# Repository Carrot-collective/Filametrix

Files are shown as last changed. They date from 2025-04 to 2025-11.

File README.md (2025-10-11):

## Carrot Collective Projects

[ERCF v3](https://github.com/Carrot-collective/ERCF_v3)

[ERCT / CottonTail](https://github.com/Carrot-collective/ERCT)

[Filametrix Toolhead Cutter Buffer](https://github.com/Carrot-collective/Filametrix)

[Blobifier Purge System](https://github.com/Carrot-collective/Blobifier)

[Filamentalist Rewinder Buffer](https://github.com/Carrot-collective/Filamentalist)

### Carrot Collective Affiliates

[Jabberwocky Toolhead](https://github.com/kinematicdigit/Jabberwocky)

[Happy Hare Wiki](https://github.com/moggieuk/Happy-Hare/wiki)

<br />

# This is a work in progres, please pardon our dust.

# Filametrix Mod


This is a mod of the Voron Stealthburner which adds a filament cutting possibility!




### Main Body
#### Main Body for old motor plate of Clockwork2
- SB_CW2_Main_Body_Cutting_with_2xD2F_ECAS
- SB_CW2_Main_Body_Cutting_with_D2F_ECAS
- SB_CS2_Main_Body_EBB_ECAS_D2F "CW2 main body for the ERCF w/ ECAs, bearing switch, and SB2209 Canbus mods" Thanks to [juliusjj25](https://github.com/juliusjj25)

#### Main Body for new motor plate of Clockwork2
Adapting to recent changes in the Clockwork2 design (July 2023) - Left new / Right old
grafik

A step with file the material removed of the motor plate is available here [Cutoff new motor plate](https://github.com/sorted01/Filametrix/blob/main/CAD/CW2_new_motor_plate/SB_CW2_cutoff_new_motor_plate.stp)

*Not all main bodys are converted yet. Use the old [motor plate](https://github.com/sorted01/Filametrix/blob/main/STL/motor_plate.stl) if your main body is not listed below.*

A more compact version using a M6 bowden fitting instead of the ECAS is also available for some main bodys. 
Additonally, a more rigid [latch](https://github.com/sorted01/Filametrix/blob/main/STL/[a]_latch_M6.stl) is available for the M6 version. (ECAS version of the latch is compatible with all M6 main bodys.)

* ECAS mount
	- SB_CW2_new_motor_plate_Main_Buddy_Cutting_with_ECAS

* M6 bowden mount
	- SB_CW2_new_motor_plate_Main_Buddy_Cutting_with_M6

#### Support for LGX Lite
https://www.printables.com/de/model/576122-lgx-lite-stealthburner-filament-cutter

tommorox234 has created the main body for the LGX Lite. Feel free to get in contact with him via printables.
Thank you :)

#### Support for StealthOrbiter
- ORBITERMOUNT_STANDARD_PG7_V2_Cutting

by [emjay276](https://github.com/emjay276)

### Printhead
#### Update for Phaetus Dragon UHF and Phaetus Dragon UHF mini
- SB_Dragon_UHF_cutting_TH_Front or SB_Dragon_UHF_mini_cutting_TH_Front
- SB_Dragon_UHF_cutting_TH_Rear or SB_Dragon_UHF_mini_cutting_TH_Rear
- Knife_holder_Dragon_UHF

by [emjay276](https://github.com/emjay276)

#### Update for Bambu Hotend has been added.
- SB_Bambu_cutting_Printhead_back
- SB_Bambu_cutting_Printhead_front or SB_Bambu_cutting_Printhead_front_2
- Bambu_Adapter

Thanks to "Jakub Kadlec" from Facebook :) 

#### Update for Voron Revo Hotend 
- SB_RevoVoron_back
- SB_RevoVoron_front

by Russell Gower - NOTE currently untested!!

#### Update for Rapido Hotend

- see folder

say thank you to [juliusjj25](https://github.com/juliusjj25)  :) 

#### Update for Slice engingeering mosquito hotend

https://www.printables.com/de/model/614813-filametrix-mod-for-slice-engingeering-mosquito-hot

say thank you to "https://www.printables.com/de/@MakeAUsername_285162"

#### Update for Revo Micro
- SB_RevoMicro_back
- SB_RevoMicro_front

by Leif Lang - NOTE: Remixed from the Official Stealthburner and the remixed version for the Revo Voron by Russel Gower

## Motivation
I was looking at the ERCF MMU for several month now. What always kept me from starting the project were the discussions about issues and problems with  filament tip forming. Suddenly a new company showed us how they do it quite reliable. They just cut the filament. Further motivated and inspired by the design of @pure100kim who has built the [ERCF_Filament_Cutting_MOD](https://github.com/pure100kim/ERCF_Filament_Cutting_MOD) I started to build my own version of it.

## See how it works

Proof of concept 1: https://youtube.com/shorts/HOMG8cVk_U4

Proof of concept 2: https://youtu.be/tTcrxttyths

Filametrix in action: https://www.youtube.com/watch?v=tfMZWQRqtvY

## Good to know

Please be aware:
- We will need to use one of the ADXL mounting threads
- Depending on the setup and position of the cutting point we will most probably not lose any build volume
- For the main body i remixed the ECAS version from [Alexanderor](https://www.printables.com/de/model/433797-clockwork-2-ecas-fitting-for-ercf)

## What you need
### Print list
#### Toolhead
- 1x SB (hotend name) cutting Printhead back
- 1x SB (hotend name) cutting Printhead front
- 1x SB Main body Cutting with ECAS (or with sensor)
- 1x SB motor plate (as Stealthburner has seen a small update the newest plate does not fit anymore. So please use the one from this git)
- 1x SB latch ECAS
- 1x Cutting arm
- 1x Knife holder

#### Cutting point on gantry
- 1x depressor mount
- 1x depressor

#### Cutting point on gantry with servo
- tbd...

### Parts list - considering you already have a Stealthburner with Dragon Hotend

#### Toolhead: 
- Loctite
- 1x M3 nut (DIN934; ideally a countersunk tool to modify the nut for proper filament insertion)
- 2x M3 washer (0.5mm)
- 1x M3x18 SHCS (it repleaces the top left M3x25 SHCS from the SB-Cover mount) 
- 2x Voron heat inserts
- 1x M3x18 FHCS (counter sunk screw)
- 1x M3x8 SHCS
- 1x M2.5x16 SHCS (15-18mm works)
- Spring 0.4x4x15 or alternative of ballpoint pen (L=15mm; D<=4,5mm) (I've ordered some for testing, to have a "defined" spring)
- Type 4 metal hobby blades (we will cut it to length) [Link](https://de.aliexpress.com/item/1005005117830095.html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) Amazon link, these need glue to be held in but work fine (USA) [Link](https://www.amazon.com/dp/B07QP8L1QG)
- 

#### Cutting point on gantry
- 1x M3x16 BHCS
- 1x M3 nut
- 1x M3x8 FHCS
- 2x M3 SHCS (Lengths: 6mm - no backers, 10mm - titanium backers, 12mm - MGN9 rails)
- 2x Voron heat inserts

## Assembly
### Cutting arm
#### Cut skalpel to length l=26mm

##### Result

#### Insert skalpel into knife holder
Insert the skalpel (which is cut to 26mm) into the knife holder until you see it in the little hole. Use pliers to push it into the knife holder. Some force should be needed as the skalpel should stay in place due to the "pressfit". If that's not the case add some glue.(Depelding on skalpel tolerances)

#### Put knife holder into cutting arm
The M2.5x15 screw is directly screwed into the plastic of the knife holder. The tip of the screw should be flush with the cutting arm or no more than 0.1-0.3mm above it.
Check the orientation of the hole for the M2.5 screw in the knife holder. It needs to be on the bottom side.

**!! The knife holder must move up and down without friction in the cutting arm but shoult not have a lot play. Maybe some grinding is needed. !!**




### Add heat inserts

Tip here for the heat set that goes above the cutter I would suggest drilling the threads out with a ~2.5mm drill bit. On the hotend holder side below the cutter make sure you flare out the PTFE tube to help guide the filament.
#### Main body

#### SB cutting Printhead back

#### Depressor - one on either end, end with ribs should be flush with surface below ribs with no plastic sticking up past surface


#### Finished cutting point assembly should look like this
Note: for titanium backers, the backer should be centered between belt clamps and the end of the depressor mount should be flush with the end of the backer. This will work for all backers with 10/20/40mm spacing with the furthest back hole 5-15mm from the end. Height of depressor should be adjusted to press in the depression on the cutting arm and the BHCS can be adjusted in and out for the right positioning and locked in place with the M3 nut.
261054978-7247e729-06e5-4cba-a8ad-aafa2b9bd7a1

I need some time to finalize assembly instructions. If you have questions you'll find me in discord "sorted#8941"

## Code

**The code only works with https://github.com/moggieuk/Happy-Hare** If you haven't updated yet you really should.

Latest version provided by [thisiscam](https://github.com/thisiscam)

I added the option to push the filament tip back into the hotend

Copy additional.cfg to your printer config directory and include it in your printer.cfg below all of the mmu includes via [include additional.cfg]

### In mmu_parameters.cfg:
set form_tip_macro: _MMU_CUT_TIP

set toolhead_extruder_to_nozzle and toolhead_sensor_to_nozzle to corresponding measured values of your toolhead.

set force_form_tip_standalone: 1

### In additonal.cfg
You will need to adjust the parameters in addtional as well, like setting up your cutter location, speeds, etc. More information in the cfg file itself.
set variable_output_park_pos: ... to the distance from the nozzle tip to the blade

#### Servo
If you are using a gantry servo, remove the hashtags related to "gantry_servo"s in this file.

# If you want to support me

paypal (https://www.paypal.com/paypalme/sorted01)

#### Optional Next location
The _MMU_CUT_TIP now has an option to move to a "next location" immediately after making the cut. For instance,  set it to the purge tower's location from the slicer. The _SET_LOC_AFTER_TOOLCHANGE sets this location, and the _MMU_CUT_TIP macro will be responsible for traveling immediately after the cut but prior to the unload. See the orcaslicer's toolchange gcode two messages down as an example. If you don't plan to use it, it's safe to ignore this point.


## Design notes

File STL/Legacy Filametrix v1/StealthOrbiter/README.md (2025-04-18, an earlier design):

Remixes below bt SaltyPaws have been tested (see attached images) with lever arm from https://www.printables.com/model/647601-orbiter-filametrix-mod.

Cutting remix by SaltyPaws using latest from https://github.com/sneakytreesnake/StealthOrbiter for mounting CANBUS or those who don't need PG7 and need their lever arm to work.

**ORBITERMOUNT_No_Sensor_V3_Cutting v2.stl**

Cutting remix by SaltyPaws no sensor version.

**ORBITERMOUNT_Sensor_V3_Cutting v2.stl**

Cutting remix by SaltyPaws as above, but now with slot for below extruder filament sensor. Note that this needs to be printed with supports painted on for the sensor section, as bridging is not sufficient here. Sensor version uses v0.1 BOM limit switches (lever microswitch) with the end of the lever trimmed to fit. It uses the metal ball from the orbitor sensor (6 mm). M2 hex bolts can be threaded straight into the plastic, or you can melt a m2 nut on the other side.

Below remixes by Charles@CharlesDahlma_340167 (https://www.printables.com/model/647601-orbiter-filametrix-mod.)

**Cutter body small.obj**
Used with all model files above

**Orbiter body Filamentrix.obj**
PG7 version

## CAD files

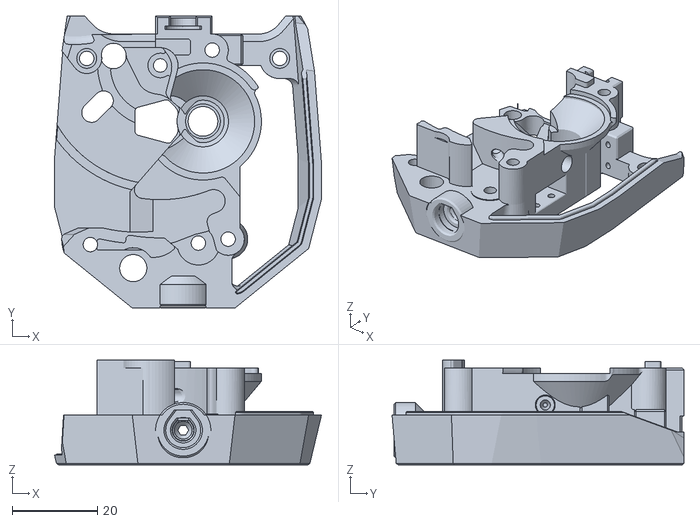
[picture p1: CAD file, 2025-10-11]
STL/CW2/CW2_Main_Body_ET_Sensors_ECAS_v3.stl
62.8 x 68.7 x 24.7

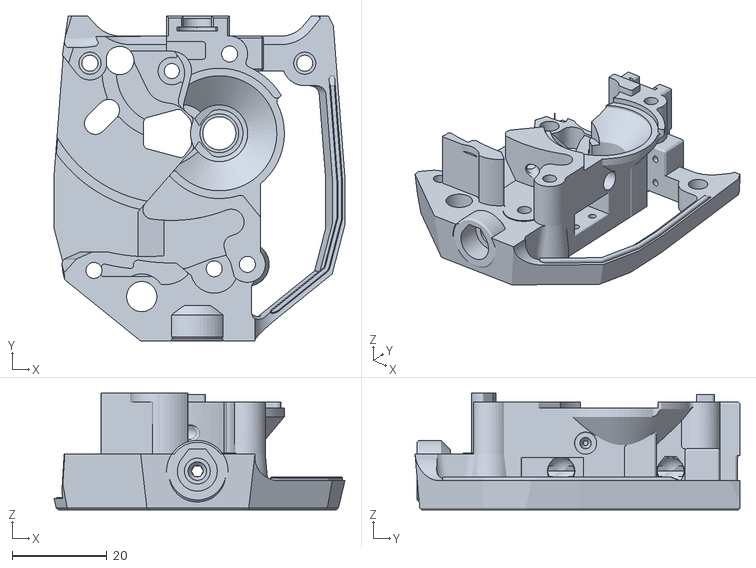
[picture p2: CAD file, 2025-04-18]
STL/CW2/CW2_Main_Body_EBB_2240_ET_Sensors_ECAS_v2.stl
61.5 x 68.7 x 24.7

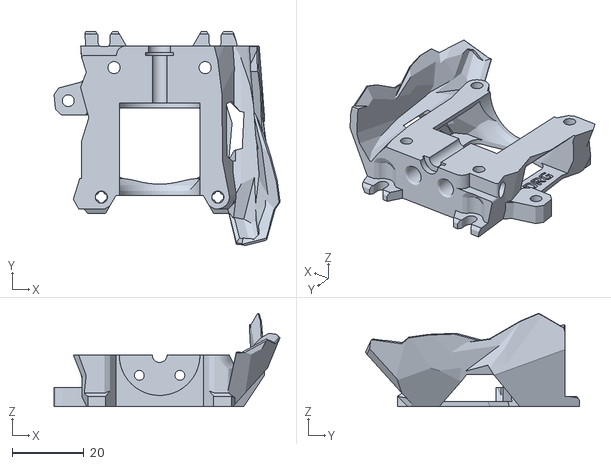
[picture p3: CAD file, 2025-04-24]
STL/Dragon HF/Filametrix_Dragon_HF_Back.stl
63.0 x 59.7 x 26.1

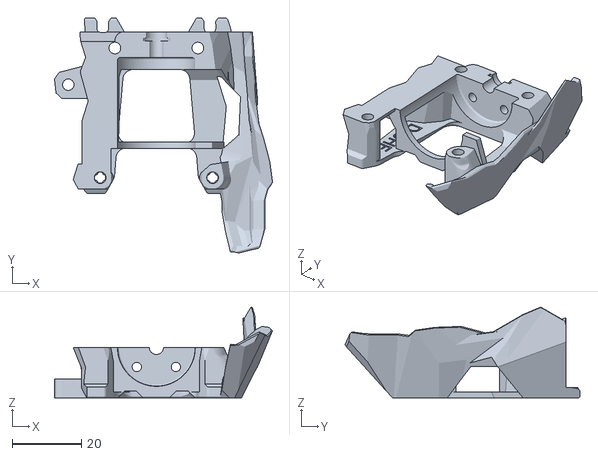
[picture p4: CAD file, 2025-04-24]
STL/Dragon UHF/Filametrix_Dragon_UHF_Back.stl
63.0 x 68.0 x 26.3

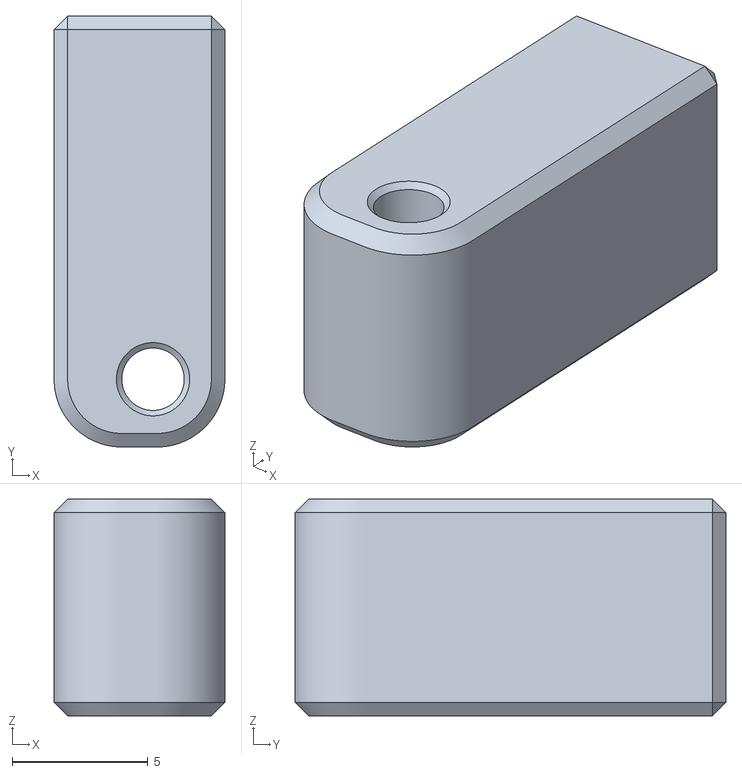
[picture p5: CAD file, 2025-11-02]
STL/Knife_holder.stl
6.30 x 15.9 x 8.00

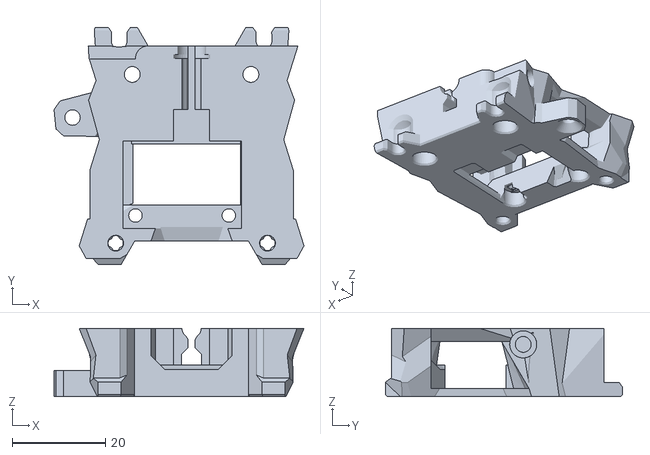
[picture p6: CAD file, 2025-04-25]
STL/StealthBurner Bambu/Filametrix_Stealthburner_Bambu_Back.stl
53.5 x 50.8 x 14.6

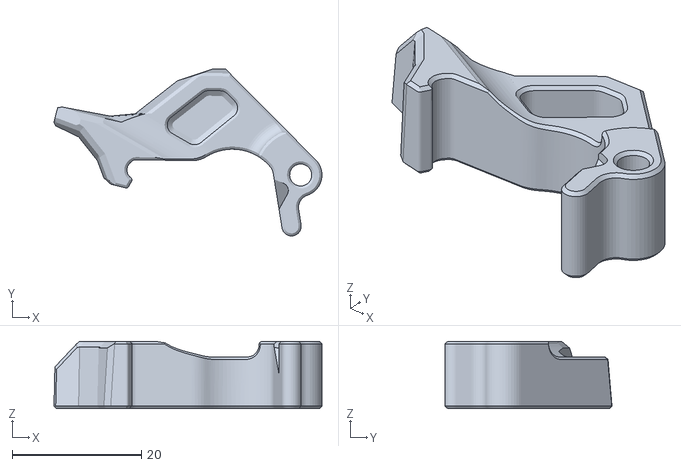
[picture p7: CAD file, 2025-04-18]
STL/[a]_Latch_v2.stl
41.5 x 25.8 x 10.4

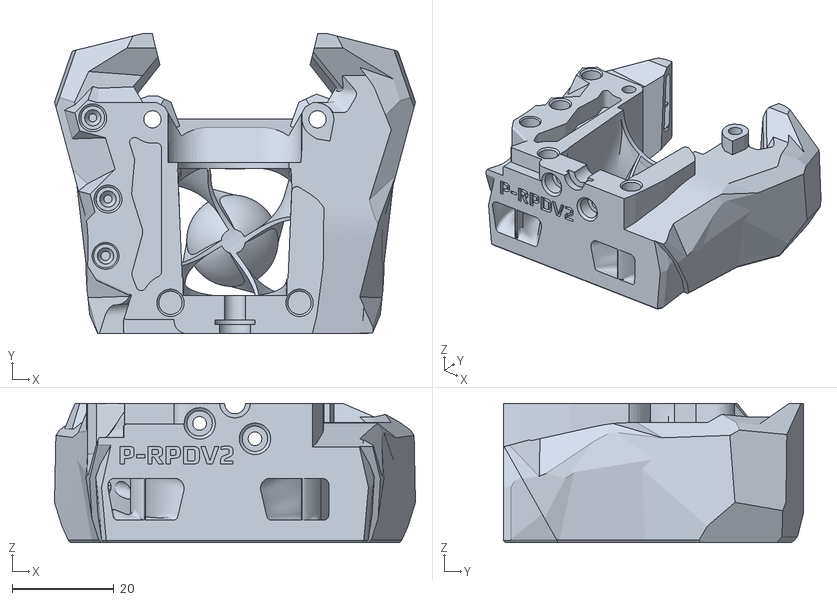
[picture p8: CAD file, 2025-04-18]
STL/Rapido/Filametrix_Rapido_v2_Front.stl
71.1 x 59.1 x 27.4

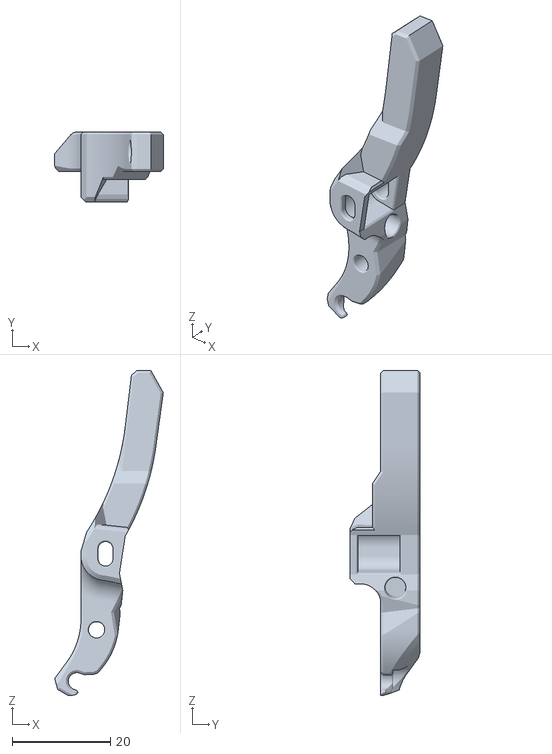
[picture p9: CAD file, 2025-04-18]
STL/Cutting_Arm.stl
22.1 x 14.2 x 66.1

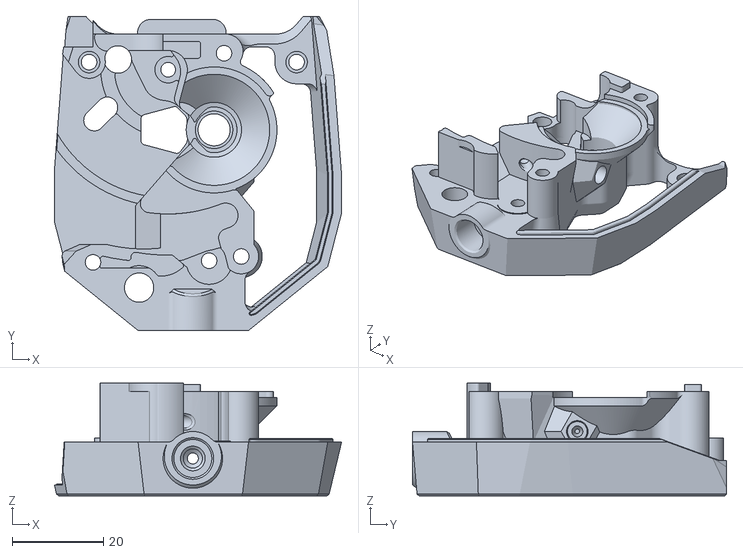
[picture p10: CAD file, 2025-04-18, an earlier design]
STL/Legacy Filametrix v1/CW2_new_motor_plate/SB_CW2_new_motor_plate_Main_Buddy_Cutting_with_ECAS.stl
62.8 x 68.7 x 24.7

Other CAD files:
STL/CW2/CW2_Main_Body_EBB_2240_ET_Sensors_ECAS.stl
STL/CW2/CW2_Main_Body_ET_Sensors_PC4-M10_v2.stl
STL/Rapido/Filametrix_Rapido_v2_Back.stl
STL/Revo/Filametrix_Revo_Back.stl
STL/Legacy Filametrix v1/CW2_old_motor_plate/SB_CW2_Main_Buddy_Cutting_with_ECAS.stl
STL/CW2/CW2_Main_Body_ET_Sensors_ECAS_v2.stl
STL/Legacy Filametrix v1/CW2_new_motor_plate/SB_CW2_new_motor_plate_Main_Buddy_Cutting_with_M6.stl
STL/Legacy Filametrix v1/CW2_old_motor_plate/SB_CW2_Main_Buddy_Cutting_with_2xD2F_ECAS fix Rev1.stl
STL/CW2/CW2_Main_Body_ET_Sensors_ECAS.stl
STL/CW2/CW2_Main_Body_ET_Sensors_PC4-M10.stl
STL/Legacy Filametrix v1/Bambu Toolhead/Bambu Adapter M5 nut.stl
STL/Legacy Filametrix v1/Bambu Toolhead/Bambu_Adapter.stl
STL/Legacy Filametrix v1/Bambu Toolhead/SB_Bambu_cutting_Printhead_back.stl
STL/Legacy Filametrix v1/CW2_old_motor_plate/SB_CW2_Main_Buddy_Cutting_with_D2F_ECAS.stl
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

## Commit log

2025-01-11 Add recreated CAD for modular Filametrix CW2.1
    My own take on Filametrix on CW2 that allows any further changes to or editions of Clockwork to be carried forward with relative ease.
2025-04-18 Move v1 files to Legacy Folder
    Moved v1 files to Legacy folder.
    [Bambu Adapter M5 nut.stl, Bambu_Adapter.stl, CW2_Main_Body_ET_Sensors_ECAS.stl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]
2025-04-18 Upload first batch of Alpha files
    Added Alpha files for Filametrix Alpha.
    [CW2_Main_Body_EBB_2240_ET_Sensors_ECAS.stl, CW2_Main_Body_EBB_2240_ET_Sensors_ECAS_v2.stl, CW2_Main_Body_ET_Sensors_ECAS.stl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]
2025-04-21 Create Modular_Toolhead_Cartridges.f3d
    Easy way to make Filametrix Toolhead Cartridges
2025-04-24 Update Dragon Filametrix
    Was previously misaligned by 0.2mm. Fixed now.
    [Filametrix_Dragon_HF_Back.stl]
2025-04-24 New Dragon UHF hotend mount
    First edition!
    [Filametrix_Dragon_UHF_Back.stl]
2025-04-25 Added StealthBurner Bambu toolhead
    Added StealthBurner Bambu toolhead
    [Filametrix_Stealthburner_Bambu_Back.stl]
2025-10-12 Revise Error in Ducting
2025-10-16 Re-Add Bearing Slots
    Thanks for deciding we don't need the bearing slots, Fusion.
